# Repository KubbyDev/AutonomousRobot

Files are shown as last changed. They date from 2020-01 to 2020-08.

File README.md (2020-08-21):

# Autonomous Robot

## Note on the current progress of the project

This is only the version 1 of the robot. I think the software could work, but there are 2 major hardware problems.  
The ultrasonic sensor is not anywhere near accurate enough, and it will probably work a lot better if I can have more than one point (currently I only have the distance to the first obstacle in front of the robot). A lidar could work well for that.  
The second problem is the accuracy of the positioning system. This version doesn't have any feedback, it only knows when and for how much time the motors where powered. It works pretty well for the first few seconds but quickly desynchronizes from reality. I should add encoders on the wheels.  
Also the communication between the Arduino and the ESP and between the ESP and the phone are slow, I should try to improve on that (Maybe use TCP instead of HTTP for the ESP-phone).  
Lastly, the Arduino is a bit underpowered to calculate paths, even with A* pathfinding. I can maybe replace it with a Teensy or use the ESP or a Raspberry pi for these high level things.

## Demo

This project is a robot that uses an ultrasonic sensor and an Arduino to create a 2D map of its environment. It is then able to use this 2D map to move from one point to another using pathfinding. To be controlled, the robot's ESP8266 hosts a Wifi network that the user can connect to using a smartphone app. The app requests and displays the 2D map of the robot and its expected position in the map. The user can then click on the place he wants the robot to move to.

For the moment the obstacle avoiding doesn't work and the map updating is really bad. But I managed to get the communication and the navigation working so I made this short demo video
Demo 1 - Navigation (https://www.youtube.com/watch?v=F6cUCP5h3g4 "Demo 1 - Navigation")

## How does this work

Software used:  
For the ESP and Arduino programs: The Arduino IDE  
For the smartphone app: Android Studio  
For the model: Blender and PrusaSlicer  

I used an Arduino Mega+Wifi which is an Arduino Mega with an ESP8266 integrated. But the project is designed to work on an Arduino Uno with a separate ESP module (Thats what I wanted to do in the beginning but I used the Mega+Wifi for simplicity). So the control program is designed to work with only 10 digital pins and only 2048 bytes of dynamic memory.

### Environment map

At each navigation update, the last distance recorded by the ultrasonic sensor is used to update the main map (if there has been a measure since the last update). All the pixels between the position of the robot and hit point are turned off and the pixel on the hit point is turned on.  

The main map is 72 by 72 pixels. If each pixel was stored in one byte, it would take 5184 bytes which is 2.5 times the max memory of the Uno. So I made an utility file to manage boolean matrices. What it does is simply use all the bits it has, by storing 8 booleans on each byte. With that solution the space used by the main map drops to 649 bytes.

There is also a second map, in lower resolution (24*24) but with numbers (unsigned char) instead of booleans and used only for the pathfinding. This map is updated at the same time as the main map, but following a different rule: Each pixel on this map is turned on if there is at least one pixel that is on in the 5x5 square at the corresponding position in the main map. For example the pixel at (5,5) in the low res map will check all the pixel between (5\*3 -1, 5\*3 -1) and (5\*3 +3, 5\*3+3) in the main map.

The sonar launches a measure every 25 milliseconds minimum (23 ms = 4 meters round trip for sound). When it starts a measure, it will just send a sound wave. Then, when the echo of the sound wave is received, the sensor will send a signal on the echo pin. The echo pin has a PCINT set up, so when the signal is received, the Arduino stops everything and calls a function. This function simply calculates the distance based on the time the sound wave took to go back to the sensor.

### Navigation

The memory space is very limited, so I had to find a pathfinding algorithm that works directly on the low res map (without storing too much things beside). The solution I came up with is not good in terms of performance but it meets this goal. The algorithm goes through the map and for each pixel, if a neighbour pixel has a distance value that is less or equal to its own distance value, it takes the neighbours pixel's value+1. And the algorithm does it repeatedly until there is no more change. The worst case scenario's complexity is n^2, but in practise it is often much faster because a lot of pixels are updated on each iteration. Also the order of the update changes between each iteration to maximise the chances of updating multiple pixels per iteration.  
Note: I added A* pathfinding to improve performance but it only works on the Mega because the Uno doesn't have enough memory

After execution of this algorithm, the low res map will have 0 on the target position, 255 on the walls and the distance to the target on every other pixel. The low res map is then used by the robot to know in which direction it has to move. It finds the pixel that has the lowest value around him and goes towards it.

To keep track of the position of the robot on the map the control algorithm has to simulate the motors. I filmed the robot during an acceleration (using SpeedCalc.ino) and then I used Avimeca (old french software) and Excel to get the speed of the robot as a function of time. I found that it accelerates linearly for the first 0.7 seconds and then goes at constant speed. So I programmed this in the PositionTracker to increase its accuracy. I also added a waiting time every time the robot changes direction to reduce inaccuracies due to residual movement.

### Control

The goal of the communication part is too make the arduino exchange data with the smartphone app.  
The arduino itself doesn't have a direct access to a wifi antenna, so we need to put an intermediary: the ESP8266. On the Mega+Wifi it is already on the board, but it is still a separated thing. To make it communicate with the Arduino we have to use Serial communication.  
So the ESP8266 hosts a webserver and a wifi network. The smartphone app can then connect to this wifi network and send HTTP requests to the web server. The ESP will receive those requests and use Serial to ask the Arduino for an answer, and send back the answer to the phone via wifi.

The ESP server can respond to 3 requests:

- /map: Returns the intern map stored on the Arduino in the form of hexadecimal digits (one digit for 4 pixels)
- /set_target?x=000&y=000: Changes the goal location of the robot
- /position: Returns the expected position and rotation of the robot in its intern map.

The smartphone app is fairly simple. It keeps a copy of the robot's map and its position in memory and dislpays it to the user. At regular intervals, it sends a position and a map request to update it. If the user clicks on the screen, it will send a set_target request with the location where the user clicked. The requests are sent with a librairy called Volley.

When the ESP receives the request, it will check for errors and then send a "command" via Serial to the Arduino. The commands that can be sent are M to get the map, P to get the position and T\<x\>,\<y\> to change the target. All the messages exchanged via Serial end by a \n.  
If the request is a set_target the response to the HTTP request will just be "Target changed" but if it is a map or a position request the ESP will record everything the Arduino sends via Serial until it finds a \n, and then send the recorded message as a response.

The Arduino is constantly listening for requests from the ESP. When it receives a request, it responds immediatly. The only important thing to note is that the writing Serial buffer is limited in size (256 bytes for the Mega I think), and the answer to a map request takes 1296+1 bytes. The solution to this problem is to make the ESP read as the Arduino writes. I even added a security in case the Arduino writes faster than the ESP can read: The Arduino writes blocks of 16 bytes and then calls flush to wait for the ESP to finish reading the current block.

## Reproduce this project

### The way I did it

You will need:

- 1 Arduino Mega with ESP module integrated  
- 1 OSOYOO Model X motors controller  
- 2 DC 3V-12V dual axis gear reducer motors (the yellow ones)  
- 1 HC-SR04 ultrasonic sensor (with support, or you will have to print it)  
- 1 Hammer wheel  
- 8 1.5V batteries with a 8 slots support or two 4 slots supports  
- 1 Switch  
- 22 M2 bolts with nuts (I used 12 mm but 8 mm is enough)
- An access to a 3D printer

If you also want to make the bonus (esthetics) part:  

- An SG90 servo motor

#### 3D Printing and Assembling

If you want to 3D print the robot you can use the 3D files in Models/. The parts in Body/ are the minimum you need to print to get the robot working. The parts in Esthetics/ are only esthetic. Thanks to Saban for the model I used for the WALL-E parts https://www.myminifactory.com/object/3d-print-wall-e-3971. You can find printing recommendations in the Models/Info/Recommendations.txt file.

The assembly is pretty hard but if you have patience and method it's doable. I recommend using a screwdriver and touching the motors with it to magnetise it so you can place bolts and nuts in the right place without too much effort.  
The 4 holes in line on the front are for the sonar. You will only use 2 but if you use an Arduino Mega you will have to use the holes that are not in the middle (you can use the ones in the middle if you use an UNO).
When placing the servo in the main box of the esthetic part, place it on the left of the supports. If you place it wrong the short arm will be too short and the long arm will be too long.

#### Software upload

First you will need to measure the robots speed. Upload the Tests/SpeedCalc/SpeedCalc.ino program in the Arduino. The robot will go forward for 3 seconds, then backwards for 3 seconds, then turn to the left for 3 seconds and turn to the right for 3 seconds. Make sure it does it in the right order. If it doesn't, invert the + and the - of the motors. Measure the distances the robot travels and the angles it makes when it turns. Then open ArduinoProgram/Data.h and put the values you found for the speed and angular speed (pay attention to the units).  
When this is done you just have to upload the code to the Arduino and the ESP.

To upload the code to the Arduino:  
On the Mega, set the switches 3 and 4 to ON, all the rest to OFF (connects the Arduino to the USB port)  
In Sketch > Include Library > Manage Librairies, install PinChangeInterrupt by NicoHood  
Make sure you selected the right board in Tools/Board.

To upload the code to the ESP:  
In File > Preferences > Additionnal Boards Manager URLS, put this: https://arduino.esp8266.com/stable/package_esp8266com_index.json  
In Tools > Board > Boards Manager, install esp8266 by ESP8266 Community  
On the Mega, set the switches 5, 6 and 7 to ON, all the rest to OFF (connects the ESP to the USB port, in firmware update mode)  
Make sure you selected the Generic ESP8266 module.

To make it run you have to set the switches 1 and 2 to ON (you can leave the 3 and 4 also ON to be able to reupload code to the Arduino without changing the switches).

#### Phone app

It is probably possible to transfer an apk or something to your phone to install the app but I don't know how to do it.  
To install the app I used Android studio. Open the ControlApp folder with android studio, plug your phone to your computer via USB (you have to activate developper mode on your phone), and press the run button. It will transfer all the necessary data to your phone and launch the app. For the next launches you don't need the computer anymore.

### Possible changes

You can replace the Mega+ESP board with a regular Mega or an Uno board with a separate ESP module. That's what I wanted to do at the beginning, but I didn't manage to upload code to the ESP with this technique (I tried to plug it to the PC with a USB adapter, and I also tried to connect it to the arduino in serial and connect the arduino to the PC. Both methods without success). If you use an Arduino Uno you will have to use the old pathfinding algorithm because the Uno doesn't have enough memory to use the A* algorithm.
The control algorithm works on the Mega+Wifi and is supposed to work on the normal Mega and on the Uno without changing the pin numbers. If you want to change anything, go to ArduinoProgram/Data.h. If you want to use a separate ESP module, you might also have to change the Serial connection to the ESP on the Arduino side. Go to ArduinoProgram/Communication.cpp and change the SERIALOBJECT.  
The holes in the robot's body can be used for an Uno or a Mega (and maybe some other board but they work for these ones).

You can replace the motors controller by another motors controller, it is not that important. But the holes in the robot models were made for this board so you might have to change them. The motors can be any type of motors but again, you might have to change the motors support model if you want to 3D print it. Just make sure they can endure 12V and they don't turn too fast.

The free wheel can be anything but you might have to modify the model so the front is at the same height as the back. It is important for the sonar (but if it is simpler for you, you can also change its angle).

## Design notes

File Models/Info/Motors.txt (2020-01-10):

2 Holes
Diameter 3mm
Distance between the centers: 1.75 cm

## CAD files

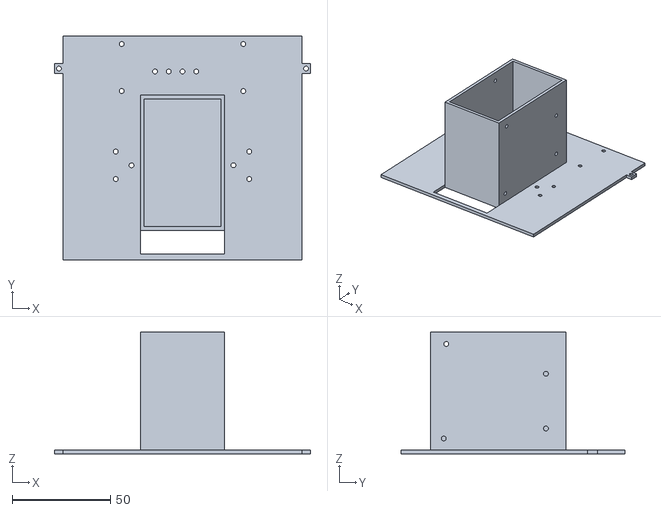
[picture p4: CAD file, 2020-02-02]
Models/Body/MainBody.stl
130.5 x 114.0 x 62.0

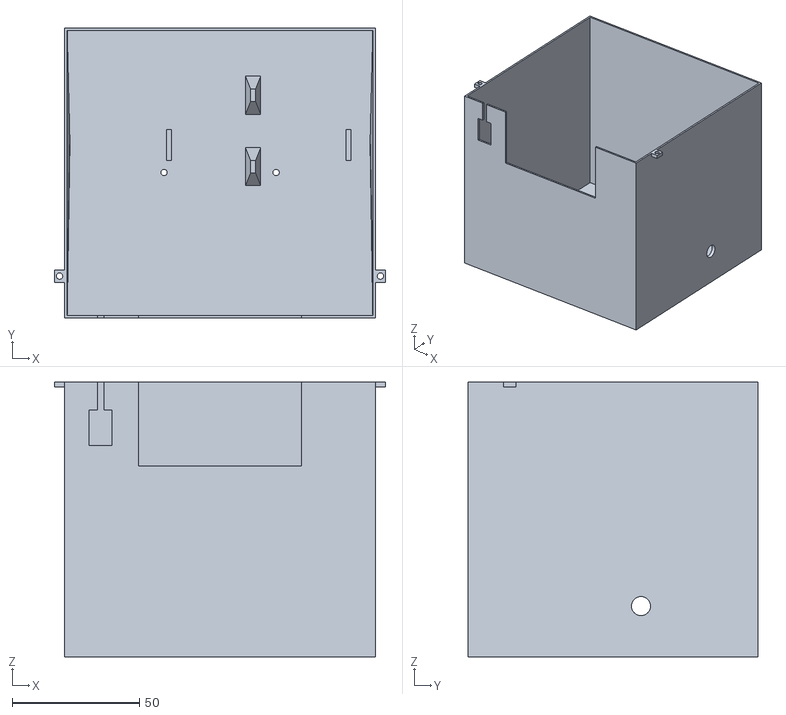
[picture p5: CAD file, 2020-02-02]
Models/Esthetics/MainBox.stl
130.0 x 114.0 x 108.0

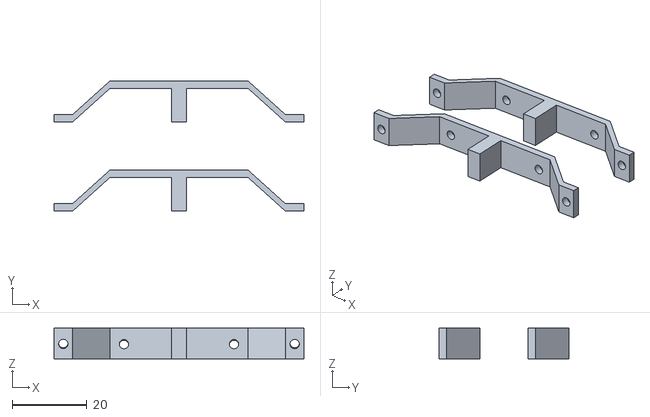
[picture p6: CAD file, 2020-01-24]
Models/Body/FreeWheelSupports.stl
67.0 x 34.9 x 8.27

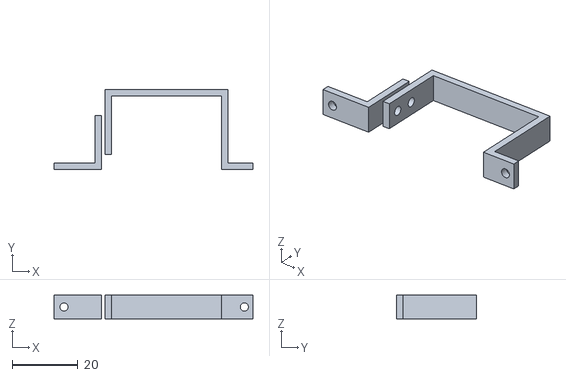
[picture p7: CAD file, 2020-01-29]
Models/Esthetics/ServoArmsAttach.stl
60.6 x 24.5 x 7.20

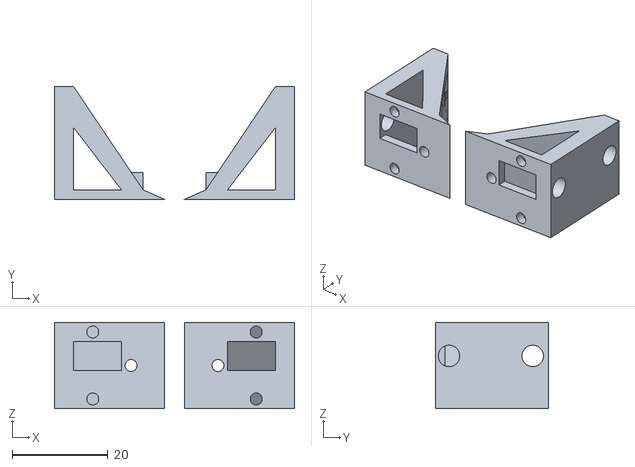
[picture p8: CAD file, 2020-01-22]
Models/Body/MotorsSupports.stl
50.2 x 23.6 x 18.0

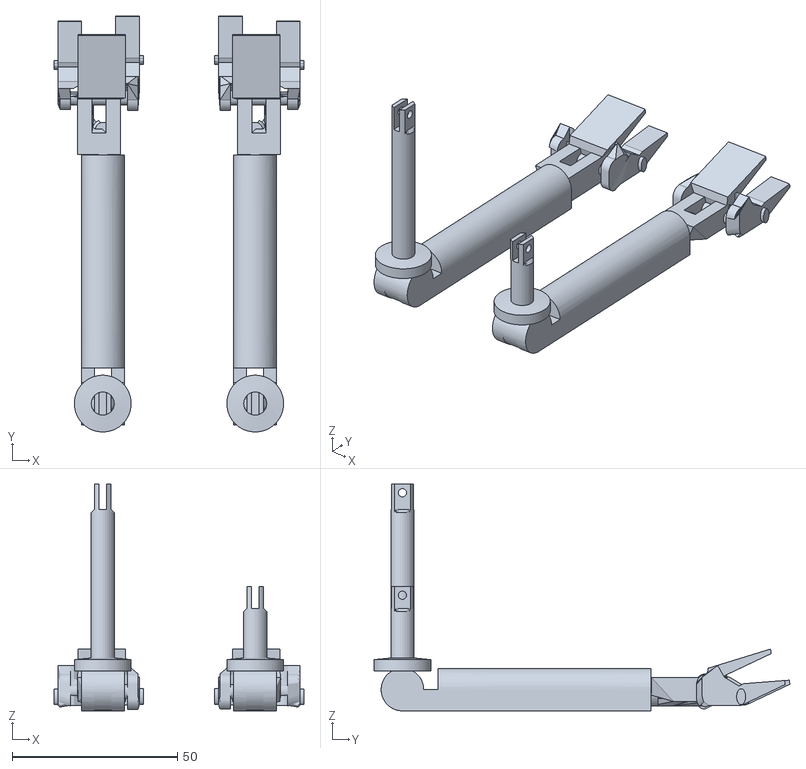
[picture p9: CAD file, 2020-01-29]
Models/Esthetics/Arms.stl
75.7 x 126.0 x 68.7

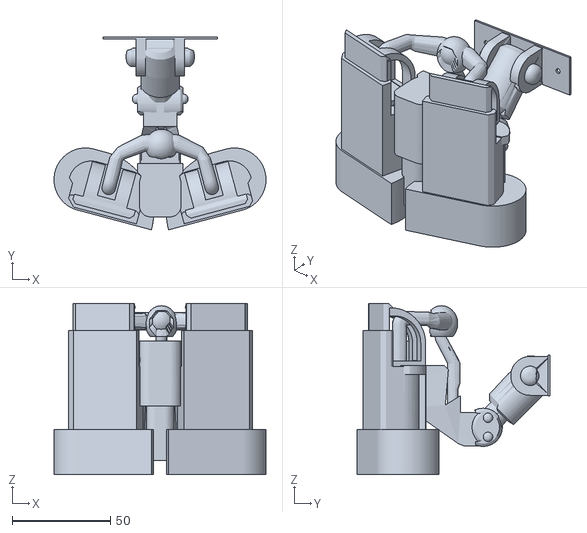
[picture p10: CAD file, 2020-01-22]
Models/Esthetics/Head.stl
107.9 x 98.1 x 87.2

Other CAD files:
Models/Body/FreeWheelSupports.blend
Models/Body/MainBody.blend
Models/Body/MotorsSupports.blend
Models/Esthetics/Arms.blend
Models/Esthetics/Head.blend
Models/Esthetics/MainBox.blend
Models/Esthetics/ServoArmsAttach.blend

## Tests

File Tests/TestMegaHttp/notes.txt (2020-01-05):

1=ON  2=ON  3=OFF 4=OFF 5=OFF 6=OFF 7=OFF 8=OFF (ATmega2560<->ESP8266)
1=OFF 2=OFF 3=ON  4=ON  5=OFF 6=OFF 7=OFF 8=OFF (USB <->ATmega2560)
1=OFF 2=OFF 3=OFF 4=OFF 5=ON  6=ON  7=ON  8=OFF (USB<->ESP8266 (Update firmware or sketch))
1=OFF 2=OFF 3=OFF 4=OFF 5=ON  6=ON  7=OFF 8=OFF (USB<->ESP8266 (communication))
1=OFF 2=OFF 3=OFF 4=OFF 5=OFF 6=OFF 7=OFF 8=OFF (All independent)

I want to marry this guy
https://forum.arduino.cc/index.php?topic=578430.0

// Step 1: Web server

Follow the steps (message from Nov 09, 2018, 11:34 pm), then when connected you should be able to connect to 192.168.0.20:80 in browser

// Step 2: Handling requests

In the ESP8266 program, add this

void handleArgs() { 
  String message = "";
  if (server.arg("Temperature") == ""){     //Parameter not found
    message = "Temperature Argument not found";
  }else{     //Parameter found
    message = "Temperature Argument = ";
    message += server.arg("Temperature");     //Gets the value of the query parameter
  }
  server.send(200, "text/html", "<h1>You are connected</h1>" + message);          //Returns the HTTP response
}
//In setup()
server.on("/args", handleArgs); //Calls handleArgs when client connects with 192.168.0.20:80/args?Temperature=0

(Done in SimpleWebServer)

// Step 3: Communication with arduino

Add serial communication, Serial3 on the Mega, Serial on the Esp 

Switch RXD3/TXD3 ON
Switches 1 to 4 ON, 5 to 8 OFF
Go to http://192.168.0.20/args?state=0 http://192.168.0.20/args?state=1

(Done in LedSwitch)

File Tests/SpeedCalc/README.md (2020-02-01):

This test script should be used to calibrate the control algorithm
First set the time to 3000 and measure the distance traveled (-> D) and the rotation made (-> R)
Then set the time to 1000 and measure the distance traveled (-> d) and the rotation made (-> r)

T and t are the times (3000 and 1000 but in seconds -> 3 and 1)

vmax = (D-d)/2
turnmax = (R-r)/2
ta = (2\*D - 6\*d)/(D - d)

Vmax should go to ROBOT_SPEED
ta should go to ACCEL_DURATION (convert it from seconds to microseconds)

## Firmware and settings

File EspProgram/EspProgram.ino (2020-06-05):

// -------------------------------------------------------------------------------------------------
//
// This code is meant to control the ESP8266. Functionnalities:
// - Hosts the Wifi network (ssid: MappingRobot, open)
// - Receives HTTP requests and checks if they are correct
// - Communicates with the Arduino via Serial to answer or serve requests
//
// Requests:
// - /map: Returns the intern map stored on the Arduino in the form 
// of hexadecimal digits (one digit for 4 pixels)
// - /set_target?x=000&y=000: Changes the goal location of the robot. 
// Numbers are in intern map coordinates
// - /position: Returns the expected position and rotation of the robot
// in its intern map.
//
// -------------------------------------------------------------------------------------------------

#include <ESP8266WiFi.h>
#include <WiFiClient.h>
#include <ESP8266WebServer.h>

#define SERIALOBJECT Serial // The serial object used to communicate with the Arduino
#define MAP_SIZE 72 // Size of the main map (should be the same here, in ArduinoProgram/Data.h and in the smarphone app)
#define TIMEOUT 1000 // Maximum waiting time for incomming data from the Arduino in milliseconds

// Errors that can be encoutered while communicating with the Arduino
#define SERIAL_NO_RESPONSE 1
#define SERIAL_RESPONSE_NOT_FINISHED 2
#define SERIAL_RESPONSE_TOO_LONG 3

// Ids of the requests. Used by handleError
#define ID_MAP 1
#define ID_SET_TARGET 2
#define ID_POSITION 3

ESP8266WebServer server(80);
const char* ssid = "AutonomousRobot"; // Name of the Wifi network. Connect to it to send HTTP requests

// Helper functions --------------------------------------------------------------------------------

// Converts an number from 0 to 15 to its hexadecimal representation
char toHex(int i) {
    return i < 10 ? i+'0' : i-10+'A';
}

// Checks if the argument is given and is a 1-3 digits positive integer
int isArgumentCorrect(String argument) {
    String value = server.arg(argument);
    if(!value)
        return 0;
    for(unsigned int i = 0; i < value.length(); i++)
        if(value[i] < '0' || value[i] > '9')
            return 0;
    return 1;
}

// Reads data from the Arduino while it is writing it
// The buffer in parameter should be big enough to contain the response without \n
// For example if the response is expected to be TEST\n it should be of length 4.
// The return value is an error code (see the to of this file for more info)
int receiveData(int* buffer, int bufferLength) {

    long startTime = millis();
    
    // Waits for the first character
    while(!SERIALOBJECT.available())
        if(millis() - startTime > TIMEOUT)
            return SERIAL_NO_RESPONSE;
    
    // Reads the stream until a \n is found
    int next = SERIALOBJECT.read();
    while(next != '\n') {
        
        // Prevents buffer overflows
        if(bufferLength <= 0)
            return SERIAL_RESPONSE_TOO_LONG;

        *buffer = next;
        buffer++;
        bufferLength--;
        
        // Waits for the next character
        while(!SERIALOBJECT.available())
            if(millis() - startTime > TIMEOUT)
                return SERIAL_RESPONSE_NOT_FINISHED;
            
        next = SERIALOBJECT.read();
    }

    return 0;
}

// Handles an error that occured while communicating with the Arduino
void handleError(int errorCode, int requestID) {

    int code;
    String message = "Error while processing ";
    if(requestID == ID_MAP) message += "/map request: ";
    if(requestID == ID_SET_TARGET) message += "/set_target request: ";
    if(requestID == ID_POSITION) message += "/position request: ";

    // Serial communication errors
    if(errorCode == SERIAL_NO_RESPONSE) {
        code = 500;
        message += "The Arduino didn't respond. ";
    }
    if(errorCode == SERIAL_RESPONSE_NOT_FINISHED) {
        code = 500;
        message += "The Arduino responded but an error occured while receiving it. ";
    }
    if(errorCode == SERIAL_RESPONSE_TOO_LONG) {
        code = 500;
        message += "The buffer used to collect the response was too small. ";
    }
    
    server.send(code, "text/plain", message);  
}

// Request handlers --------------------------------------------------------------------------------

// Returns the intern map (cells are grouped by 8 and sent as the hexadecimal
// representation of these 8 bits. So each group is encoded as 2 characters from 0 to F)
// Query is of this form: /map
void getMap() { 

    // Sends a request to the Arduino to get the map 
    SERIALOBJECT.write("M\n", 2);

    // Gets the response from the Arduino
    int* res = (int*) malloc(sizeof(int) * MAP_SIZE*MAP_SIZE/8);
    int error = receiveData(res, MAP_SIZE*MAP_SIZE/8);

    // Sends an error message if there is an error
    if(error != 0) {
        handleError(error, ID_MAP);
        free(res);
        return;
    }

    // Formats the received data to sends it back in the HTTP response
    String result = "";
    for(int i = 0; i < MAP_SIZE*MAP_SIZE/8; i++) {
        result += toHex(res[i]/16);
        result += toHex(res[i]%16);
    }

    server.send(200, "text/plain", result);
    free(res);
}

// Sets the new target position of the robot
// Query is of this form: /set_target?x=000&y=000
void setTarget() {
    
    // Stops if one of the argument is not given or not a number
    if(!isArgumentCorrect("x") || !isArgumentCorrect("y")) {
        server.send(422, "text/plain", "Bad arguments. Query is of this form: /set_target?x=000&y=000");
        return;
    }
    // Sends the numbers to the Arduino
    String message = "T" + server.arg("x") + "," + server.arg("y") + "\n";
    SERIALOBJECT.write(message.c_str(), message.length());
    server.send(200, "text/plain", "Target changed");
}

// Returns the position and rotation of the robot
// Query is of this form: /position
void getPosition() {
    
    // Sends the command to the Arduino
    SERIALOBJECT.write("P\n", 2);

     // Gets the response from the Arduino
    int* res = (int*) malloc(sizeof(int) * (15+1+15+1+15));
    int error = receiveData(res, 15+1+15+1+15);

    // Sends an error message if there is an error
    if(error != 0) {
        handleError(error, ID_POSITION);
        free(res);
        return;
    }

    String result = "";
    for(int i = 0; i < 15+1+15+1+15; i++)
        result += (char) res[i];

    server.send(200, "text/plain", result);
    free(res);
}

void notFound() {
    server.send(404, "text/plain", server.uri() + ": Not found");
}

// Main functions ----------------------------------------------------------------------------------

void setup() {

    SERIALOBJECT.begin(250000);
    IPAddress local_IP(192,168,0,20); //Connect to this IP to send HTTP requests
    IPAddress gateway(192,168,0,1);
    IPAddress subnet(255,255,255,0);
    WiFi.softAPConfig(local_IP, gateway, subnet);
    WiFi.softAP("ESPsoftAP_01");
    WiFi.softAPIP();

    WiFi.softAP(ssid);
    server.on("/map", getMap);
    server.on("/set_target", setTarget);
    server.on("/position", getPosition);
    server.onNotFound(notFound);
    server.begin();
}

void loop() {
    server.handleClient();
}

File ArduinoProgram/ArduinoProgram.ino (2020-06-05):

// ----------------------------------------------------------------------------------------------------------
//
// Program of the Arduino board. Functionnalities:
// - Navigates to the target position. The low res map is used to find a path to it
// - Makes sonar measurements and updates the intern map and the low res map
// - Answers the requests of the ESP via Serial (give the intern map or the position, change the target position)
// - Manages the servo for the arms
//
// ----------------------------------------------------------------------------------------------------------

#include "Data.h"

#include "Navigation.h"

#include "Motors.h"
#include "Sonar.h"
#include "Servo.h"

#include "Communication.h"

#include "BooleanMatrix.h"
#include "UCharMatrix.h"
#include "Vector.h"

void setup() {

    Serial.begin(115200);
  
    // Empties the internMap and the low resolution map
    bm_clear(internMap);
    clearMatrix(lowResMap);
    vectorSet(position, MAP_SIZE/2, MAP_SIZE/2);
    vectorSet(target, MAP_SIZE/2, MAP_SIZE/2);

    // Initialises the motors and the sonar
    initMotors();
    initSonar();

    // Initialises the communication with the ESP8266
    initCommunication();

    // Initialises the servo for the arms
    initServo();
}

void loop() {

    DBG Serial.println("NEW LOOP --------------------------------------------------------------------------------------------");

    // Updates the communication with the ESP8266
    // (Retrives or sends information to the user if necessary)
    updateCommunication();

    // Updates the control program and the motors
    // (Changes the values in Data.cpp)
    updateNavigation();

    // Lauches a new sonar measurement
    updateSonar();

    // Updates the arms position
    updateServo();
}

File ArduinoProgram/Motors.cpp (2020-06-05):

#include "Motors.h"
#include "Data.h"
#include "Tools.h"

#include <Arduino.h>

// Speed control ------------------------------------------

// Sets the speed of each motor (an integer between -255 and 255)
void setSpeed(int leftSpeed, int rightSpeed) {

    // The speed should always be between -255 and 255
    clamp(&leftSpeed, -255, 255);
    clamp(&rightSpeed, -255, 255);

    // Sets the direction of rotation for each motor
    digitalWrite(IN1, rightSpeed > 0);
    digitalWrite(IN2, rightSpeed < 0);
    digitalWrite(IN3, leftSpeed > 0);
    digitalWrite(IN4, leftSpeed < 0);

    if(leftSpeed == 0 && rightSpeed == 0) {
        // Brakes if the speed of both motors are 0
        digitalWrite(ENA, HIGH);
        digitalWrite(ENB, HIGH);
    }
    else {
        // Otherwise, sets the speed for each motor
        analogWrite(ENA, abs(rightSpeed));
        analogWrite(ENB, abs(leftSpeed));
    }
}

// High level control functions -----------------------------

void forward() {
    setSpeed(   LEFT_MOTOR_SPEED,   RIGHT_MOTOR_SPEED);
}

void backward() {
    setSpeed( - LEFT_MOTOR_SPEED, - RIGHT_MOTOR_SPEED);
}

void turnLeft() {
    setSpeed(   LEFT_MOTOR_SPEED, - RIGHT_MOTOR_SPEED);
}

void turnRight() {
    setSpeed( - LEFT_MOTOR_SPEED,   RIGHT_MOTOR_SPEED);
}

void idle() {
    setSpeed(0, 0);
}

// Init ----------------------------------------------------

void initMotors() {
    pinMode(IN1, OUTPUT); 
    pinMode(IN2, OUTPUT); 
    pinMode(IN3, OUTPUT);
    pinMode(IN4, OUTPUT); 
    pinMode(ENA, OUTPUT);  
    pinMode(ENB, OUTPUT);
    idle();
}

// Update -------------------------------------------------

// Updates the motors speeds according to the forwardInput and the turnInput
void updateMotors() {

    if(fabsf(turnInput) > 0.1f) {
        if(turnInput < 0)
            turnRight();
        else
            turnLeft();
    }
    else { 
        if(forwardInput > 0)
            forward();
        else if(forwardInput < 0)
            backward();
        else
            idle();
    }
}

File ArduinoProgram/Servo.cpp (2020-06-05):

#include "Servo.h"
#include "Data.h"

#include <Arduino.h>
#include <Servo.h>

Servo servo;
unsigned long lastChangeTime; // The last arms position change moment (ms)

void initServo() {
    servo.attach(SERVO_PIN);
    servo.write(SERVO_MAX);
    lastChangeTime = millis();
}

void updateServo() {

    DBG Serial.println("Updating Servo ----------------------");

    // Does nothing if the position already changed shortly before
    if(millis() - lastChangeTime < SERVO_PERIOD)
        return;

    lastChangeTime = millis();

    // If the robot is not going forward, the arms will just go down
    if(forwardInput < 0.1f) {
        servo.write(SERVO_MAX);
        return;
    }
    
    // Else the arms will move up and down
    // Goes to the min angle if the current angle is higher than the middle, max otherwise
    int current = servo.read();
    if(current > (SERVO_MIN+SERVO_MAX)/2)
        servo.write(SERVO_MIN);
    else
        servo.write(SERVO_MAX);
}

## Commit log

2020-01-05 Move from the Arduino repo
2020-01-10 Robot model for 3D print v1
    [body.blend]
2020-01-10 Files ready for printing
    [Part1.blend, Part1.stl, Part2.blend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]
2020-01-16 Small changes + Fix map update
    [Data.h, InternMap.cpp, Motors.cpp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]
2020-01-22 Communication improvements + Fixes
    [ArduinoProgram.ino, Communication.cpp, Data.h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]
2020-01-22 Robot model v2
    [All.blend, Part1.blend, Part1.stl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]
2020-01-29 Models fixes
    [All.blend, Part6.blend, Part6.stl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]
2020-01-30 Big Control algorithm improvements and fixes
    [ArduinoProgram.ino, Data.h, InternMap.cpp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]
2020-01-30 Fixes and improvements on the control algorithm
    [Data.h, InternMap.cpp, Motors.cpp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]
2020-01-31 Rename models
    [Arms.blend, Arms.stl, FreeWheelSupports.blend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]
